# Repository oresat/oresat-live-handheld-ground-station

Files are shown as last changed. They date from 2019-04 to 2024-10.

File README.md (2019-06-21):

# Introduction
The OreSat Live Handheld Ground Station (HGS) project provides everything you need to build your own ground station capable of receiving images transmitted from OreSat in Low Earth Orbit.  HGS is designed to be inexpensive, easy to assemble, and simple to use so that it can be built by Middle and High School students.  The entire design is open source to encourage reuse and experimentation.

HGS is a portable unit built around a high gain directional antenna. Using a mobile phone application to locate OreSat, you aim the antenna to get the best possible signal. The live images are then received by the groundstation, error corrections are applied and the image is made available to any WiFi capable device through a built-in web page.

OreSat HGS act as a wifi access point providing an unsecured wireless network named "OreSatLive".  Devices identify the network as a hotspot requiring the user to sign-in for Internet access.  To view the image stream simply:
1. Connect your wifi to the "OreSatLive" network
2. Choose to sign-in when prompted
3. The OreSat Live web interface will open automatically

HGS was created for use with the OreSat mission, but it is designed to be used by any group interested in long range image transmission.  The handheld ground stations can be reused for other cubesat or balloon launches.

Once the final design is completed, users will be able to purchase all of the required parts as a kit from https://www.crowdsupply.com/

# HGS Parts List
All of the required parts to build HGS can be found in the Bill of Materials [(BOM)](BOM.md)

# Hardware Setup
Build your Handheld Ground Station kit according to the [Assembly Instructions](hgs-model/assembly-instructions/OreSat_Live_HGS_Assembly.pdf)

# Software Setup
1. [Download the SD card image oresat_hgs_14_jun_2019.img](https://drive.google.com/a/pdx.edu/uc?id=1BvP8ltkEwoBRSbCfQXceEiuxpVhkSf37&export=download)
2. Write the SD card image to a 2GB or larger card.  The [Raspberry Pi documentation](https://www.raspberrypi.org/documentation/installation/installing-images/) explains the procedure.

# Startup Procedure
1. Install the SD card in Raspberry Pi
2. Insert phone into the holder
3. Connect Raspberry Pi power cable to the USB power bank
4. Load Satellite AR app on phone and select OreSat
5. Point the ground station in the direction of OreSat
3. Connect your viewing devices to the "OreSatLive" wifi network

# Design Details
## Software Design
If you would like to build the software system from source follow the [Build Instructions](software/BUILD.md)

## Mechanical Design
You can 3D print all of the [mechanical parts](hgs-model/README.md)  

## Circuit Board Design
The integrated antenna backplane and matching network [circuit board design files](backplane/README.md)

# Related Projects
[OreSat Live](https://github.com/oresat/oresat-dxwifi-software) for software and firmware used on OreSat satellite

[Mini OreSat](https://github.com/oresat/oresat-live-mini-oresat) combines the OreSat Live software with a Raspberry Pi Zero W + Pi Camera to create platform for hobbyist and classroom experiments with high-altitude ballooning.

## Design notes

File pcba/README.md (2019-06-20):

# Backplane for Handheld Ground Station
Schematic files for the backplane, including impedence matching circuit for connecting the antenna to the rest of the components.

Schematic files created using KiCad 5.1.2.
- **.pro** to open up Kicad project
- **.kicad_pcb** for the PCB layout
- **.kicad_mod** for the individual footprints

## Microstrip Dimensions
Backplane material: FR-4 PCB material, 0.5 oz copper, 1.58 mm thick, Er 4.34 @ 1 GHz
Note: Do not remove any of the copper ground plane on the other side of the board beneath the traces.  

Microstrip widths for various impedances:
```
50 ohm
	Width:  3.05184 mm
	Length: Arbitrary

83 ohm?
	Width: 1.20938 mm
	Length: Arbitrary

140 ohm
	Width:  0.238155 mm
	Length: Arbitrary
```

## 1/4 Wave Matching Transformer Design:
	Start at connector
	Arbitrary length of 50 ohm
	Lambda/4 length (17.7623 mm) of 83.66 ohm
	Arbitrary length of 140 ohm
	End at the helix element

## Other notes
[Source for Raspberry Pi Zero footprint dimensions](http://www.electronics-lab.com/raspberry-pi-zero-footprint-and-dimensions/)\
[Source for wf-np9202 footprint dimensions](https://www.aliexpress.com/item/wireless-net-card-LAN-NIC-module-AR9271-150M-wireless-LAN-net-card-industrial-module/32746090657.html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)

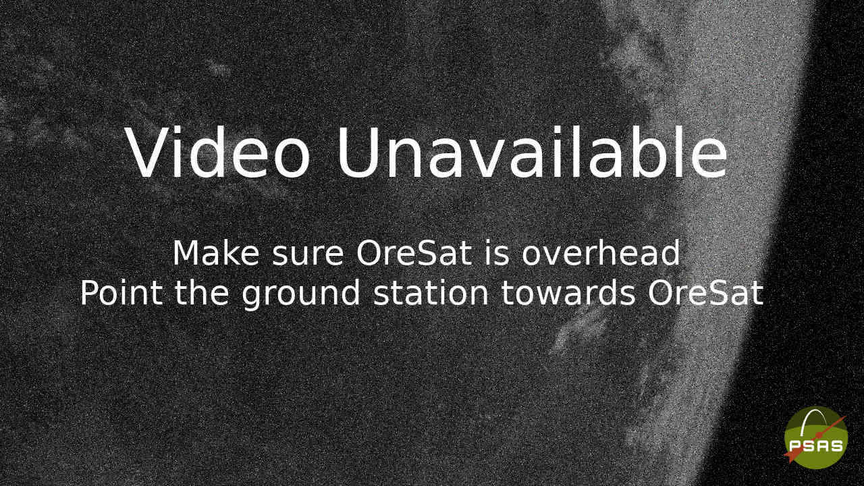
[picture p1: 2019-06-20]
software/rootfs/var/www/html/assets/img/stream_error.jpg

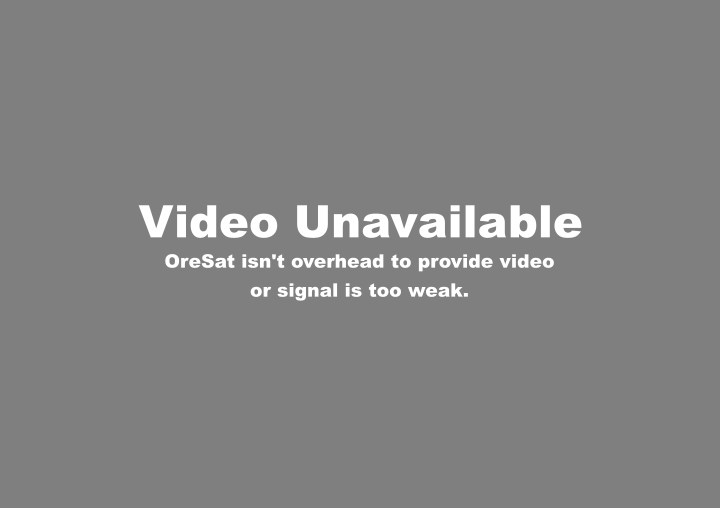
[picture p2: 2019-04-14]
software/rootfs/var/www/html/assets/img/stream_error.png

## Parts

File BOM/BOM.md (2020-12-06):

# OreSat Handheld Ground Station Bill of Materials

## Hardware
| Qty | Description | Source | Manufacturer | Part Number  |
|-----|---|---|---|---|
| 4 | #8-32 x 1 in screws and hexnuts | Home Depot | Everbilt | 460 626 |
| 4 | #8-32 x 1.5 in screws and hexnuts | Home Depot | Everbilt | 461 400 |
| 7 | #2-56 x 3/8 Nylon Screw | Frys | Waldom | FN-816-0025P |
| 7 | #2-56 Nylon Lock Nut | Frys | Waldom | FN-502-0025P |
| 7 | #2-56 Nylon hex nut | Frys | Waldom | FN-853-0025P |
| 63" | 20AWG magnet wire | Frys | Philmore | 12-1220 |

Items for easy clamping while gluing or for assembly without glue:

| Qty | Description | Source | Manufacturer | Part Number  |
|-----|---|---|---|---|
| 4 | #8-32 x 5 in Threaded Rod | Mcmaster-Carr | N/A | 91565A335 |
| 3 | #8-32 2 1/2 in Female Threaded Standoff | Mcmaster-Carr | N/A | 91115A831 |
| 2 | #8-32 Steel Hex Nut | Mcmaster-Carr | N/A | 90480A009 |

If you wish to use metric fasteners you can substitute #2-56 for M2 and #8-32 for M4

1/4-20 hex nut for tripod mounting

1.5in Hook-and-loop (velcro) adhesive backed

Foam Tape - Camper Seal 3/16in x 1 1/4in

Rubber band of your choosing

## Plastic Components
Handle

Screw Block

Phone Holder Base

Phone Holder Slide

Battery Holder

Antenna Sections (8)

Antenna Top Cap

Antenna Bottom Cap

## Electronics
Raspberry Pi Zero W

Atheros Module

USB Micro B to Atheros module custom cable 

6" USB A to Micro B power cable

5000 mAh USB power bank

## Circuit Board Components
8.2pF 0402 1% tolerance capacitor

U.FL SMD connector

75mm U.FL to U.FL coax cable

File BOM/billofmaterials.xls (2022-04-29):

PART NUMBER | DESCRIPTION | QTY. | Cost ($USD)
FASTENERS:
90480A009 | #8-32 HEX NUT | 12 | 0.198
93135A015 | #2-56 X 3/8" NYLON SCREW | 6 | 0.3468
90604A199 | #8-32 x 1" SCREW | 10 | 0.918
94812A111 | #2-56 NYLON HEX NUT | 6 | 0.4284
1/4"-20 HEX NUT | OPTIONAL: FOR TRIPOD MOUNTING | 1 | 0.0303
 | TOTAL FASTENER COST: | 1 | 1.9215
3D PRINTED PARTS:
Phone&BatteryHolderTopv2 | 3D PRINT: SLIDING PHONE HOLDER | 1 | 9.76
Phone&BatteryHolderBottomv2 | 3D PRINT: PHONE AND BATTERY HOLDER | 1 | 14.17
Handle_V3 | 3D PRINT: HANDLE | 1
HelicalAntennaSegments | 3D PRINT: ANTENNA SEGMENT 2 | 1 | 15.80
HelicalAntennaSegments | 3D PRINT: ANTENNA SEGMENT 3 | 1 | 15.85
HelicalAntennaSegments | 3D PRINT: ANTENNA SEGMENT 4 | 1 | 15.39
HelicalAntennaSegments | 3D PRINT: ANTENNA BASE (SEGMENT 1) | 1 | 17.28
Phone&BatteryHolderBasev3 | 3D PRINT: BASE TO PHONE HOLDER | 1 | 7.29
bracket | 3D PRINTED BRACKET FOR HANDLE | 1 | 7.14
 | TOTAL 3D PRINT COST: |  | 102.68
MISC:
iphone 6 | PHONE FOR USE | 1
75 MM U.FL TO U.FL COAX CABLE |  | 1
63" OF 20-GAUGE MAGNET WIRE |  | 1
MICRO USB TO WIRELESS MODULE CONNECTOR CABLE |  | 1
6" USB A TO MICRO B CABLE |  | 1
Power Bank | 5000mAh BATTERY WITH USB | 1
1.5" HOOK AND LOOP VELCRO ADHESIVE | FOR BATTERY HOLDER | 1
FOAM TAPE | FOR PHONE HOLDER | 1
RUBBER BANDS | FOR PHONE HOLDER | 2
reflectorgroundplane | OSHPARK PCB | 1
RaspberryPiZeroW | RASPBERRY PI ZERO W | 1 | 10.00
AR9271Chip | WF-NP9202 ATHEROS WIRELESS MODULE | 1

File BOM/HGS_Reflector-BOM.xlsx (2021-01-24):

Bill Of Materials for OreSat Live Handheld ground Station PCBA
Last modified: 2020/01/07
PCB version: 2.0 |  |  | P/DNP = | Place/Do Not Place (DNP is for final production boards)
BOM revision: 0 |  |  | Generic = | Any generic part with the same characteristics are OK (e.g., bypass cap)
Cnt | Part References | P/DNP | Mfg | Mfg PN | Description | Generic | Dist | Dist Part Number
4 | C1, C11, C9, C21 |  |  |  | 0603 100p
7 | C2, C5, C10, C12, C13, C17, C20 | P | Yageo | CC0603KRX5R7BB105 | 1µF ±10% 16V Ceramic Capacitor X5R 0603 | Y | Digi-Key | 311-1444-1-ND
6 | C3, C4, C6, C14, C18, C19 | P | ?? | ?? | 0402 100p | N
2 | C7, C15 | P | ?? | ?? | 0603 10n | Y
2 | C8, C16 | P | ?? | ?? | 0603 2.2u | Y
3 | E1, E2, E5 | P | Murata | BLM18GG471SZ1D | 470 Ohms @ 100Mhz 1 Signal Line Ferrite Bead 0603 200mA 1.3Ohm | Y
2 | E3, E4 | P | Murata | BLM18DN381SZ1D | 380 Ohms @ 100Mhz 1 Ferrite Bead 0603 850mA | Y
1 | J1 | P | TE Connectivity | 1909763-1 | U.FL (UMCC) Connector Jack | Y | Digi-Key | A118077CT-ND
1 | J2 | P | ?? | PRT-00587 | USB type Mini-B Connector | Y | Mouser | 474-PRT-00587
1 | J3 | P | JST | SM06B-SRSS-TB(LF)(SN) | Connector Header SMT, RA 6 pos 1.00mm | Y
2 | J5, J6 | P | Amphenol | 132134-10 | SMA Connector Jack, Female Socket 50Ohm SMT | Y | Mouser | 523-132134-10
1 | J7 | P | SparkFun | PRT-09011 | SparkFun Accessories USB Female Type A SMD Connector | Y | Mouser | 474-PRT-09011
2 | L1, L2 | P | ?? | ?? | L3216C 10n | N
2 | L3, L4 | P | ?? | ?? | L3216C 8n | N
2 | LED1, LED2 | P | Rohm | SML-E12M8WT86 | Green 572nm LED Indication - Discrete 2.2V 0603 | Y | Digi-Key | 511-1584-1-ND
1 | PCBA1 | P | Aliexpress | WF-NP9202WF | AR9721 based WiFi transciever | N
1 | PCBA2 | P | Raspberry Pi | RASP_PI_0WPI_0W | Raspberry Pi Zero W | N
5 | R1, R2, R3, R5, R6 | P | Yageo | RC0603JR-070RL | RES SMD 0 OHM JUMPER 1/10W 0603 | Y | Digi-Key | 311-0.0GRCT-ND
1 | R4 | P | ?? | ?? | 0402 150 | Y
2 | R7, R9 | P | Yageo | RC0603FR-071KL | RES SMD 1K OHM 1% 1/10W 0603 | Y | Digi-Key | 311-1.00KHRCT-ND
2 | U1, U2 | P | TI | LP2985IM5X-3.3/NOPB | Linear Voltage Regulator IC 1 Output 150mA SOT-23-5 | N | Digi-Key | 296-18476-2-ND
1 | U3 | P | Mini-Circuits | NCS3-272+ | Signal Conditioning 1:3 LTCC Transformer, 2250 - 2725 Mhz, 50 ohms | N
2 | U4, U5 | P | Qorvo | QPQ1907SR | Signal Conditioning Coexist BAW FILTER 2402.5 - 2481.5 Mhz | N
2 | U6, U7 | P | Qorvo? | TP3M9037? | LNA? | N | Mouser | 772-TQP3M9037
1 | CABLE1 | P | JST | A06SR06SR30K51A | 6 Position Cable Assembly Rectangular Socket to Socket, Reversed 0.167' (50.80mm, 2.00") | Y | Digi-Key | 455-2999-ND
Rev | Date | Notes
2.0r0 | 2020-01-07 | First revision of the BOM for v2 PCB

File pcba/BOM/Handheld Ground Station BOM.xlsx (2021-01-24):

Count | Ref Des | Value | MFR | MPN | Description | Size | Generic? | Digi-Key Part No. | Mouser Part No. | Mini-Circuits Link
4 | C1, C11, C9, C21 | 100 pF | Murata | GCM1885C1H101JA16D | CAP CER 100PF 50V C0G/NP0 0603 | 0603 | Y | 490-4767-1-ND
7 | C2, C5, C10, C12, C13, C17, C20 | 1 uF | Yageo | CC0603KRX5R7BB105 | CAP CER 1UF 16V X5R 0603 | 0603 | Y | 311-1444-1-ND
6 | C3, C4, C6, C14, C18, C19 | 100 pF | Murata | GCM1555C1H101JA16D | CAP CER 100PF 50V C0G/NP0 0402 | 0402 | Y | 490-10669-1-ND
2 | C7, C15 | 10 nF | Murata | GCD188R71H103KA01D | CAP CER 10000PF 50V X7R 0603 | 0603 | Y | 490-17738-1-ND
2 | C8, C16 | 2.2 uF | Murata | GRM188R61E225KA12D | CAP CER 2.2UF 25V X5R 0603 | 0603 | Y | 490-10731-1-ND
3 | E1, E2, E5 | BLM18GG471SZ1D | Murata | BLM18GG471SZ1D | FERRITE BEAD 470 OHM 0603 1LN | 0603 | Y | 490-16658-1-ND
2 | E3, E4 | BLM18DN381SZ1D | Murata | BLM18DN381SZ1D | FERRITEBEAD SMD Z100MHZ=380OHM 8 | 0603 | Y | 490-18574-1-ND
1 | J1 | U.FL | TE Connectivity | 1909763-1 | CONN UMCC JACK STR 50OHM SMD |  | Y | A118077CT-ND
1 | J2 | USB_MINI-B_SMT | SparkFun | PRT-00587 | USB Mini-B SMD Connector |  | Y |  | 474-PRT-00587
1 | J3 | SM06B-SRSS-TB(LF)(SN) | JST Sales America Inc. | SM06B-SRSS-TB(LF)(SN) | CONN HEADER SMD R/A 6POS 1MM |  | Y | 455-1806-1-ND
2 | J5, J6 | 132134-10 | Amphenol RF | 132134-10 | CONN SMA JACK STR 50 OHM SMD |  | Y | ARF2755-ND
1 | J7 |  | SparkFun | PRT-09011 | USB Female Type A SMD Connector |  | Y |  | 474-PRT-09011
2 | L1, L2 | 10nH | Pulse Electronics Network | PE-1206CD100JTT | FIXED IND 10NH 1A 80 MOHM SMD | L3216C | Y | 1840-1138-1-ND
2 | L3, L4 | 8nH | Murata | LQW31HN8N8J03L | Fixed Inductors 1206 8.8nH +/-5% | L3216C | Y |  | 81-LQW31HN8N8J03L
2 | LED1, LED2 | GREEN | Rohm Semiconductor | SML-E12M8WT86 | LED GREEN DIFFUSED 0603 SMD | 0603 | Y | 511-1584-1-ND
1 | PCBA1 | WF-NP9202WF | Aliexpress | WF-NP9202WF | AR9721 based WiFi transciever |  | N
1 | PCBA2 | RASP_PI_0W | Raspberry Pi | RASP_PI_0WPI_0W | Raspberry Pi Zero W |  | N
5 | R1, R2, R3, R5, R6 | 0 | Yageo | RC0603JR-070RL | RES SMD 0 OHM JUMPER 1/10W 0603 | 0603 | Y | 311-0.0GRCT-ND
1 | R4 | 150 | Panasonic Electronic Components | ERJ-2RKF1500X | RES SMD 150 OHM 1% 1/10W 0402 | 0402 | Y | P150LCT-ND
2 | R7, R9 | 1k | Yageo | RC0603FR-071KL | RES SMD 1K OHM 1% 1/10W 0603 | 0603 | Y | 311-1.00KHRCT-ND
2 | U1, U2 | LP2985XX-N | TI | LP2985IM5X-3.3/NOPB | IC REG LINEAR 3.3V 150MA SOT23-5 |  | N | LP2985IM5X-3.3/NOPBCT-ND
1 | U3 | NCS3-272+ | Mini-Circuits | NCS3-272+ | 1:3 LTCC Transformer, 2250 - 2725 MHz, 50Ω |  | N |  |  | https://www.minicircuits.com/WebStore/dashboard.html?model=NCS3-272%2B
2 | U4, U5 | QPQ1907 | Qorvo | QPQ1907SR | Signal Conditioning Coexist BAW FILTER |  | N |  | 772-QPQ1907SR
2 | U6, U7 | LNA-TQP3M9037 | Qorvo | TQP3M9037 | RF Amplifier 1.5-2.7GHz |  | N |  | 772-TQP3M9037
1 | CABLE1 |  | JST Sales America Inc. | A06SR06SR30K51A | JUMPER 06SR-3S - 06SR-3S 2" |  | N | 455-2999-ND

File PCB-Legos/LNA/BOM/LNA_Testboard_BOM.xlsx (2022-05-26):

HGS LNA Test Board
Last modified: 2022/05/22
PCB version: 1.0
BOM revision: 0
Cnt | Part References | P/DNP | Mfg | Mfg PN | Description | Generic | Dist | Dist Part Number
6 | C2,C6,C7,C9,C13,C14 | P | Murata | GRM0335C1E101JA01D | 0603 100p | Y | Mouser | 81-GRM0335C1E101JA1D
5 | C3,C8,C10,C15,C17 | P | Yageo | CC0603KRX5R7BB105 | 1µF ±10% 16V Ceramic Capacitor X5R 0603 | Y | Digi-Key | 311-1444-1-ND
2 | C4,C11 | P | TDK | C0603X5R1A103M030BA | 0603 10n | Y | Mouser | 810-C0603X5R1A103M
2 | C5,C12 | P | TDK | C1608X7S1C225K080AE | 0603 2.2u | Y | Mouser | 810-C1608X7S1C225K08
2 | E1, E2, | P | Murata | BLM18GG471SZ1D | 470 Ohms @ 100Mhz 1 Signal Line Ferrite Bead 0603 200mA 1.3Ohm | Y | Mouser | 81-BLM18GG471SZ1D
1 | J4 | P | SparkFun | PRT-00587 | USB Mini-B SMD Connector | Y | Mouser | 474-PRT-00587
3 | J1,J2,J3 | P | Cinch | 142-0701-801 | SMA 50 Ohm End Launch Jack Receptacle -Round Contact | Y | Mouser | 530-142-0701-851
2 | L2, L4 | P |  |  | L3216C 10n | N
2 | L1, L3 | P |  |  | L3216C 8n | N
1 | LED1 | P | Rohm | SML-E12M8WT86 | Green 572nm LED Indication - Discrete 2.2V 0603 | Y | Digi-Key | 511-1584-1-ND
6 | R1,R2,R3,R4,R5,R7 | P | Yageo | RC0603JR-070RL | RES SMD 0 OHM JUMPER 1/10W 0603 | Y | Digi-Key | 311-0.0GRCT-ND
1 | R6 | P | Yageo | RC0603FR-071KL | RES SMD 1K OHM 1% 1/10W 0603 | Y | Digi-Key | 311-1.00KHRCT-ND
2 | U1, U2 | P | TI | LP2985AIM5-3.3/NOPB | Linear Voltage Regulator IC 1 Output 150mA SOT-23-5 | N | Mouser | 926-2985AIM53.3/NOPB
2 | U3, U6 | P | Qorvo | QPQ1907SR | Signal Conditioning Coexist BAW FILTER 2402.5 - 2481.5 Mhz | N | Mouser | 772-QPQ1907SR
2 | U2, U5 | P | Qorvo | TQP3M9037 | LNA | N | Mouser | 772-TQP3M9037
Rev | Date | Notes
1 | 2022-05-22

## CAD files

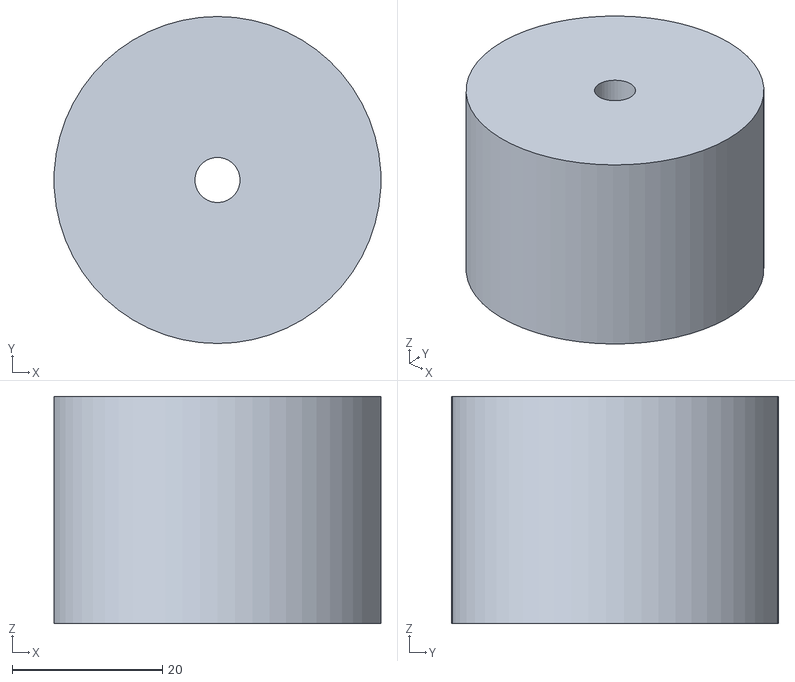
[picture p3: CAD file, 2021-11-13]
build/HelicalAntennaSegmentCap.STL
43.4 x 43.5 x 30.2

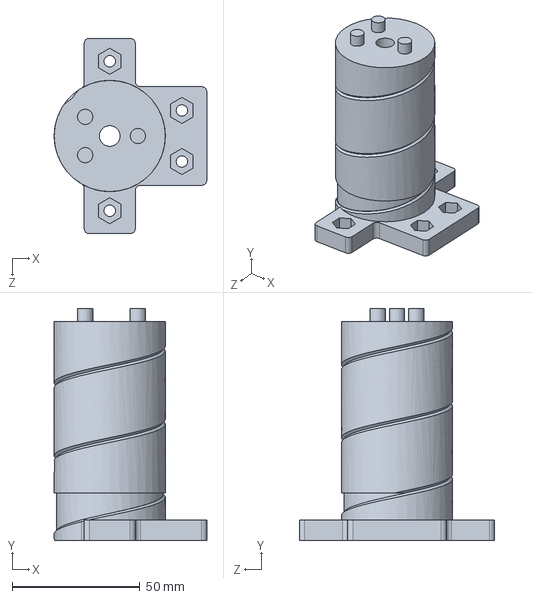
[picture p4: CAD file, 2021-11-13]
mechanical/antennaSegments/helicalAntennaSegment.SLDPRT
59.8 x 90.8 x 76.5 mm

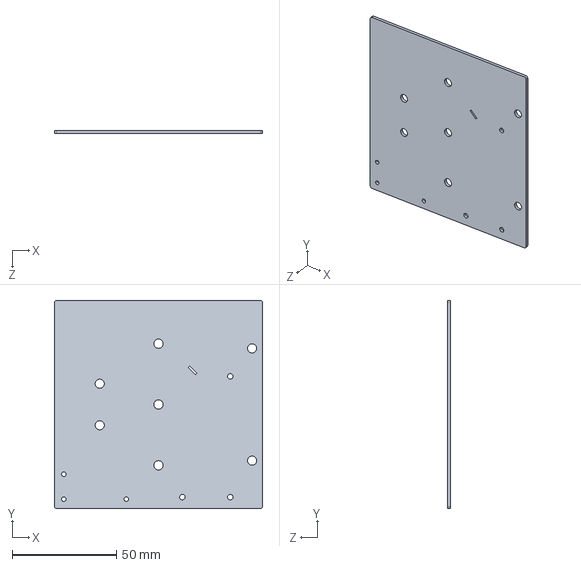
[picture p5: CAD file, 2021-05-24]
mechanical/electricalComponents/groundStationBackplane.SLDPRT
100.0 x 100.0 x 1.60 mm

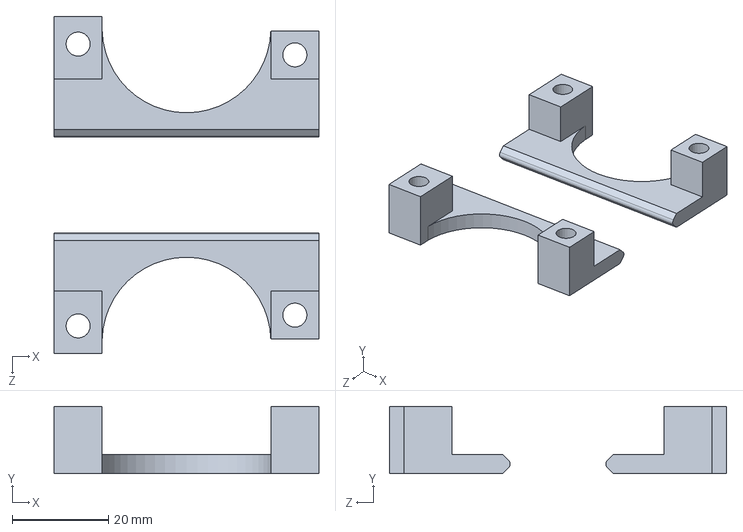
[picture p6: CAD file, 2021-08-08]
mechanical/handleAssembly/phoneClampBracket.SLDPRT
55.0 x 14.0 x 70.0 mm

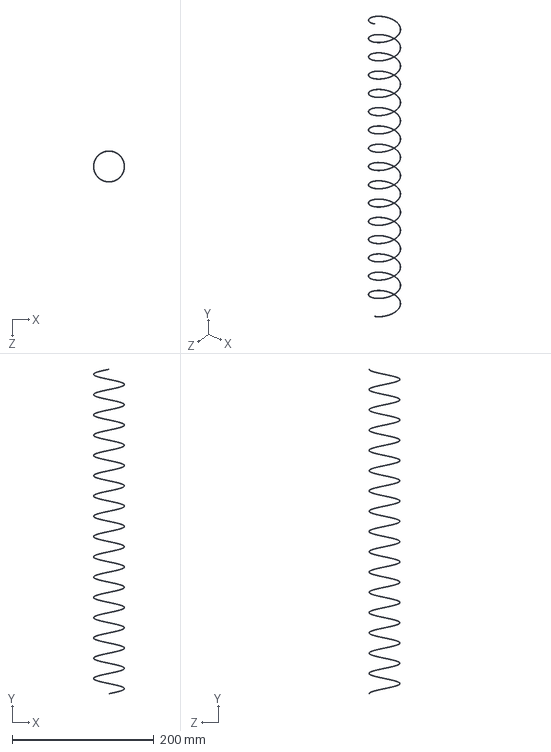
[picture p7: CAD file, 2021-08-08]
mechanical/modelParts/helicalAntenna.SLDPRT
44.3 x 458.4 x 44.3 mm

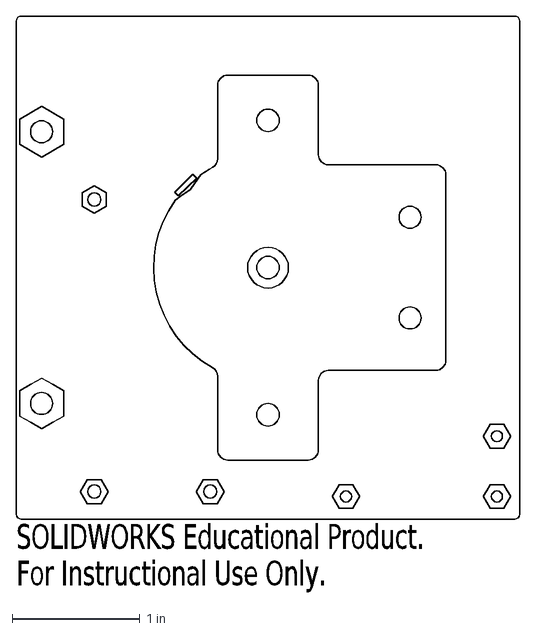
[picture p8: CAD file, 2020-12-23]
pcba/DXF/keepoutAntennaSide.DXF
SOLIDWORKS Educational Product.
For Instructional Use Only.

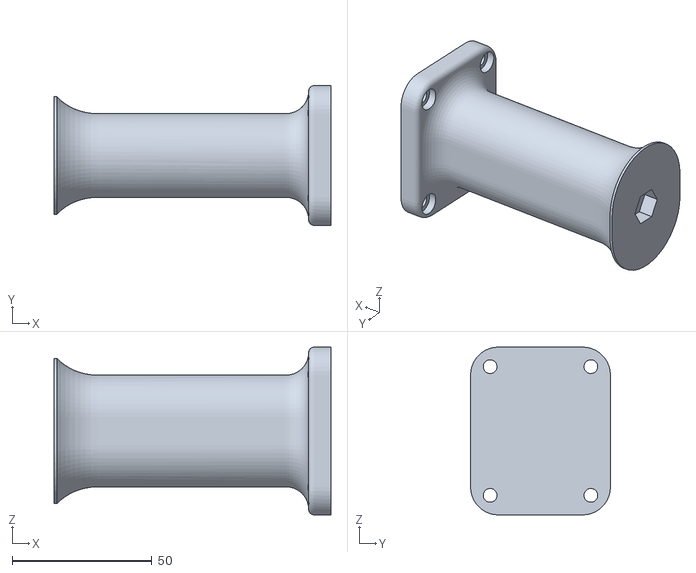
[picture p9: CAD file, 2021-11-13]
build/handle.STL
99.0 x 50.0 x 60.0

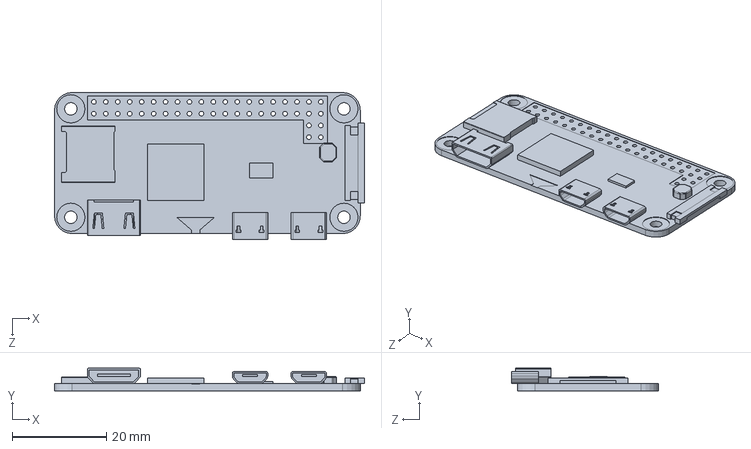
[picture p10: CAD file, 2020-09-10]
mechanical/electricalComponents/RaspberryPiZeroW.SLDPRT
65.9 x 4.80 x 31.2 mm

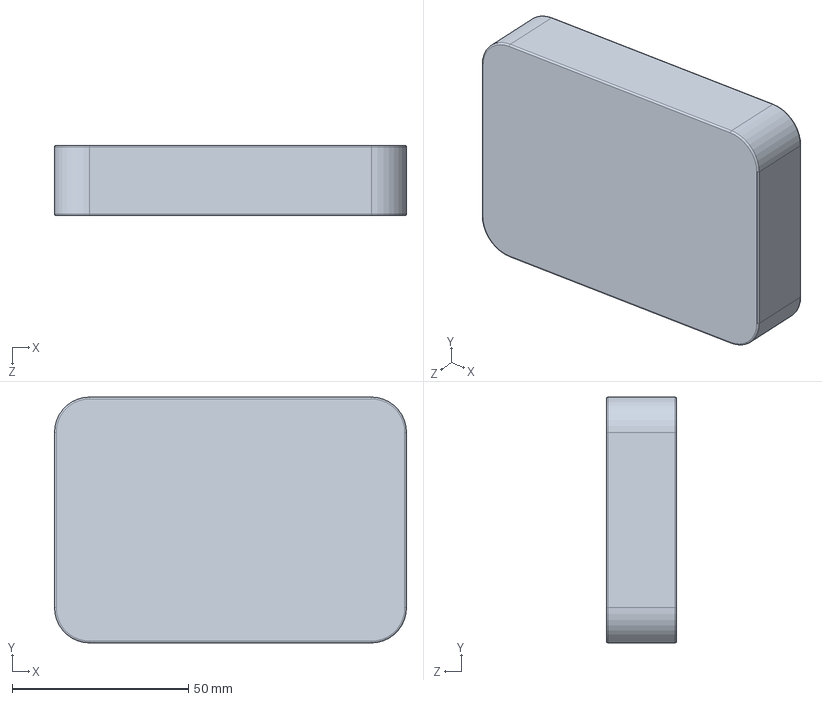
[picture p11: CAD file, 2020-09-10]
mechanical/modelParts/batterypack.SLDPRT
100.0 x 69.8 x 20.0 mm

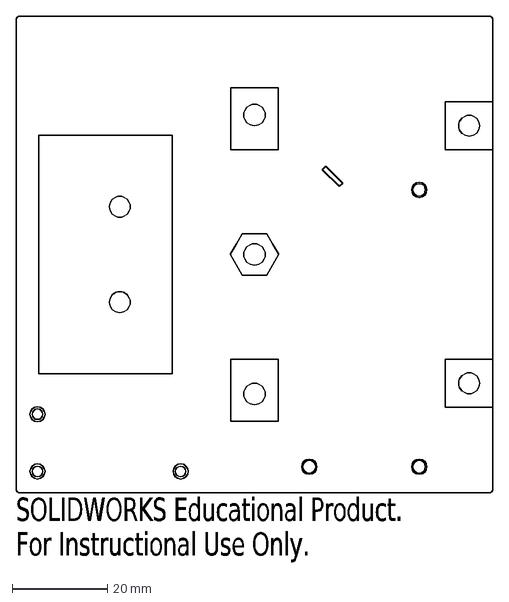
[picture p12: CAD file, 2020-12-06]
pcba/DXF/keepout.DXF
SOLIDWORKS Educational Product.
For Instructional Use Only.

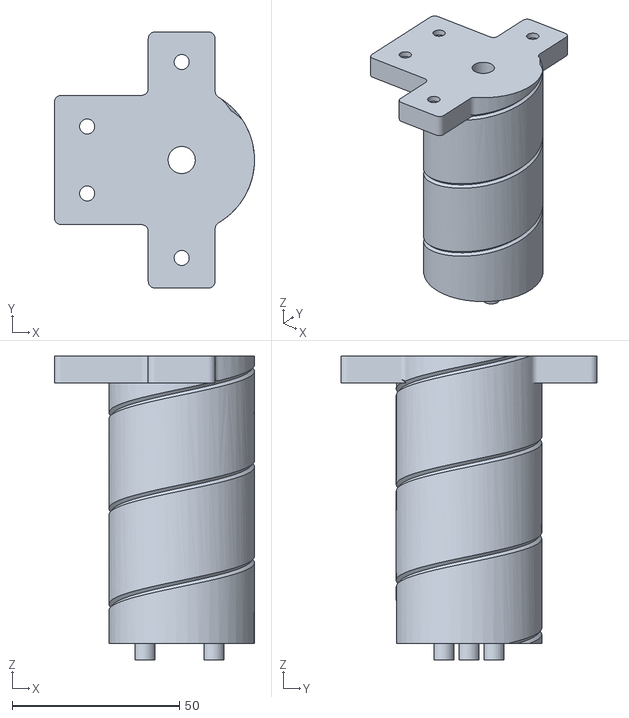
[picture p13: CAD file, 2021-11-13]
build/helicalAntennaSegmentBase.STL
59.7 x 76.5 x 90.8

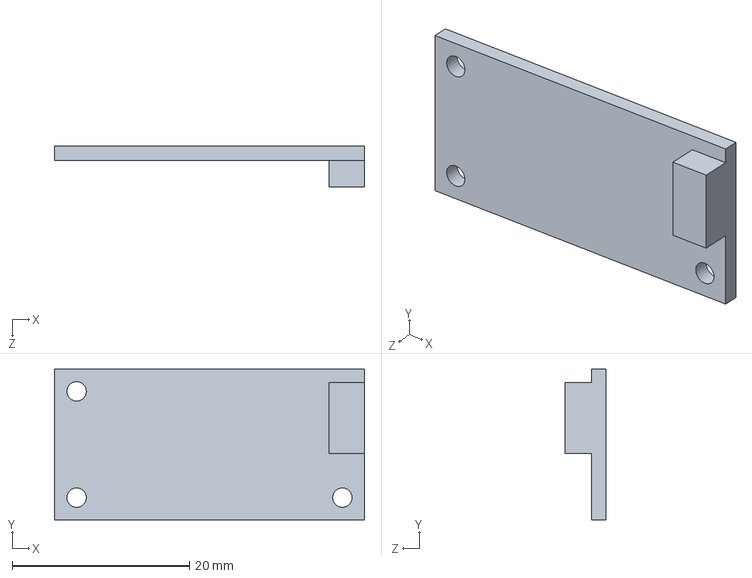
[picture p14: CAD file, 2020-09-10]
mechanical/electricalComponents/AR9271Chip.SLDPRT
35.0 x 17.0 x 4.60 mm

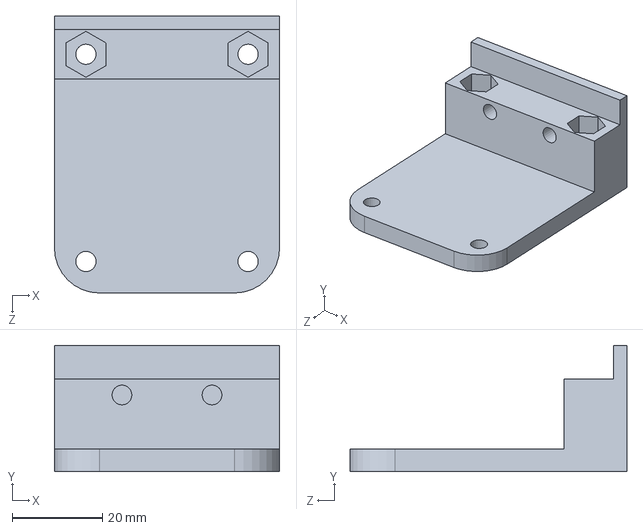
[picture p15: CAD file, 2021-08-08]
mechanical/handleAssembly/bracket.SLDPRT
50.0 x 28.0 x 61.5 mm

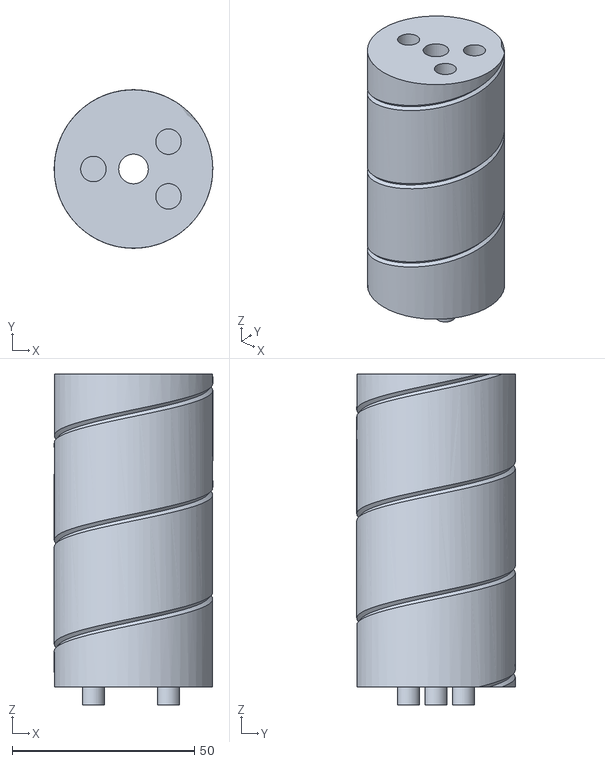
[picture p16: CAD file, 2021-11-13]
build/helicalAntennaSegmentStandard.STL
43.5 x 43.5 x 90.8

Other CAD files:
mechanical/antennaSegments/helicalAntennaSegmentCap.SLDPRT
mechanical/handleAssembly/handle.SLDPRT
mechanical/handleAssembly/handleBracketBottom.SLDPRT
build/bracket.STL
build/handleBracketBottom.STL
build/handleBracketTop.STL
build/helicalAntennaSegment-22.STL
build/phoneClampBracket-1.STL
mechanical/COTS/#8-32 nylock.sldprt
mechanical/COTS/90604A199_PAN HEAD COMBINATION DRIVE MACHINE SCREW.SLDPRT
mechanical/COTS/92319A679_FEM THRDED HEX STANDOFF.SLDPRT
mechanical/COTS/93135A015_NYLON PAN HEAD MACHINE SCREW.SLDPRT
mechanical/COTS/93225A675_Aluminum Threaded Rod.SLDPRT
mechanical/COTS/94435A509_ALUMINUM THREADED ROD.SLDPRT
mechanical/COTS/94639A460_NYLON UNTHREADED SPACERS.SLDPRT
mechanical/COTS/94812A111_NYLON 6-6 HEX NUT.SLDPRT
mechanical/handleAssembly/handleBracketTop.SLDPRT

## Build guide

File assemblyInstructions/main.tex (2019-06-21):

% Date of the last edit of these instructions
\def \lastedit{June 20, 2019}

\documentclass[paper=a4,parskip=full+]{scrartcl}
\usepackage[utf8]{inputenc}
\usepackage{titletoc}
\usepackage[margin=1in]{geometry}
\usepackage{float}
\usepackage{parskip}
\usepackage{graphicx}
\graphicspath{ {Images/} }

\title{OreSat Live HGS Assembly}
\date{Last Edited: \lastedit}

\begin{document}

\maketitle
\tableofcontents

\section{Introduction}
This document provides instructions for assembling the Handheld Ground Station with a kit.
\section{Overview of Required Materials}
\subsection{The Kit}
The kit comes with the following items:
\begin{itemize}
    \item Back-plane Circuit board
    \item 75mm U.FL to U.FL Coax Cable
    \item 63" of 20-gauge Magnet Wire
    \item Raspberry Pi Zero W
    \item WF-NP9202 Atheros Wireless Module
    \item Micro USB to Wireless Module Connector Cable
    \item 6" USB A to Micro B Cable
    \item 5000mAh Battery with USB
    \item $1/4$"-20 nut for tripod mounting
    \item 1.5" Hook-and-loop Velcro (adhesive-backed)
    \item Plastic Components
    \begin{itemize}
        \item Handle
        \item Screw Block
        \item Phone Holder Base
        \item Phone Holder Slide
        \item Battery Holder
        \item Antenna Sections x4
        \item Antenna Top Cap
        \item Antenna Bottom Cap
    \end{itemize}
\end{itemize}

\subsubsection{Board Check}
Please check that the backplane board comes with both a U.FL connector and a 8.2pF capacitor already soldered on to the board. 
% PICTURE HERE of microstrip, U.FL connector and pF cap soldered on board

\subsection{Parts Not Provided}
The parts below are not a part of the kit but still needed to assemble the HGS.\\
\textbf{*Note: You DO NOT have to use the sources specified in these tables.}
\begin{table}[H]
    \footnotesize
    \begin{tabular}{|l|l|l|l|l|}
        \hline
        Quantity & Description & Source & Manufacturer & Part Number\\
        \hline
        \hline
        4 & \#8-32 x 1" Screws and Hex Nuts & Home Depot & Everbilt & 460 626 \\
        \hline
        4 & \#8-32 x 1.5" Screws and Hex Nuts & Home Depot & Everbilt & 461 400 \\
        \hline
        7 & \#2-56 x 3/8 Nylon Screw & Frys & Waldom & FN-816-0025P \\
        \hline
        7 & \#2-56 Nylon Lock Nut & Frys & Waldom & FN-502-0025P \\
        \hline
        7 & \#2-56 Nylon Hex Nut & Frys & Waldom & FN-853-0025P \\
        \hline
        & Foam Tape - Camper Seal 3/16" x 1 1/4" & & & \\
        \hline
        1 & Rubber Band of your choosing & & & \\
        \hline
        
    \end{tabular}
    \label{tab:my_label}
\end{table}

\noindent The following are optional items for easy clamping while gluing or assembly without glue:

\begin{table}[H]
    \footnotesize
    \begin{tabular}{|l|l|l|l|l|}
    \hline
    Quantity & Description & Source & Manufacturer & Part Number\\
    \hline
    \hline
    1 & \#8-32 x 18 in threaded rod & Home Depot & & \\
    \hline 
    1 & 1/8in x 1 in fender washer & Home Depot & Everbilt & 210 364 \\
    \hline 
    1 & \#8-32 wing nuts & Home Depot & Everbilt & 934 917 \\
    \hline 
    \end{tabular}
\end{table}

\noindent You can substitute \#2-56 for M2 and \#8-32 for M4.

\newpage
\section{Assembly Instructions}
Do these things!
\subsection{Overview}
The core of the HGS is the circuit board/antenna back-plane, all the other components are in some way attached to it. The main electrical component we are concerned with is the wire wrapping the main antenna. It is soldered on the board to an impedance matching strip, strung through a hole in the board, wrapped around the antenna, and epoxied under a cap at the tip. For this reason the initial steps must be done in a particular order to ensure ease of assembly.

\subsection{Assemble antenna segments (no caps)}
First we will epoxy together the four antenna segments, without the end-caps.

(A threaded rod may be used to replace the epoxy. If using a threaded rod, ignore the sections about epoxying things, and in the section about winding the wire, use the threaded rod to hold everything together other than the cap, and clamp down the rod once the wire is wound.)

(For each section using epoxy, follow the manufacturers instructions for mixing, usage, and cure times. Make sure not to mix so much at one time that it starts to set before you have time to apply it all!)

Mix together a small batch of epoxy and apply it liberally to the end of one of the antenna segments, then insert the peg of another segment and apply pressure until the epoxy has set. Repeat until all four sections are connected as one antenna.

Make sure to wipe off any excess epoxy after clamping, to avoid filling the grooves.

\begin{figure}[H]
    \centering
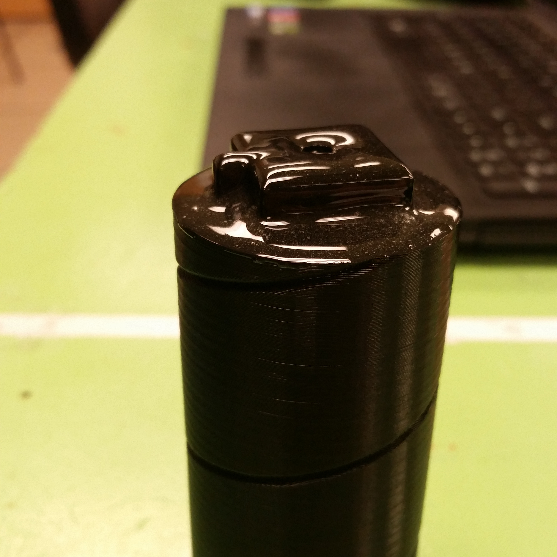
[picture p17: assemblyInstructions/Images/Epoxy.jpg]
     
    %Photo of epoxy covered antenna cap.
\end{figure}

%PHOTO OF ASSEMBLED ANTENNA

\subsection{Solder antenna wire onto micro-strip pad}
Solder one end of your wire to the bare end of the micro-strip, holding the wire perpendicular to the micro-strip. Snip off any excess wire.

Stick the rest of the wire through the nearby hole to the other side of the board for winding later.

%PHOTO HERE OF SOLDERED BOARD CLOSEUP

\subsection{Epoxy antenna to circuit board}
(Skip this section if using a threaded rod.)

Apply epoxy liberally to the peg end of the antenna, and the hollow end of the antenna clamp, push the antenna through the board, leaving the antenna on the side opposite the micro-strip, put the clamp piece on the end of the peg, sandwiching the circuit board, and clamp until the epoxy is set.

%PHOTO OF BOARD WITH ANTENNA

\subsection{Wind antenna with wire}
Take the antenna, and pulling tight against the soldered end, wrap the wire around the antenna rod, following the groove.

When the wire reaches the top, push it into the groove at the top around the tie-off peg and pull tight. (See photo.)

\begin{figure}[H]
    \centering
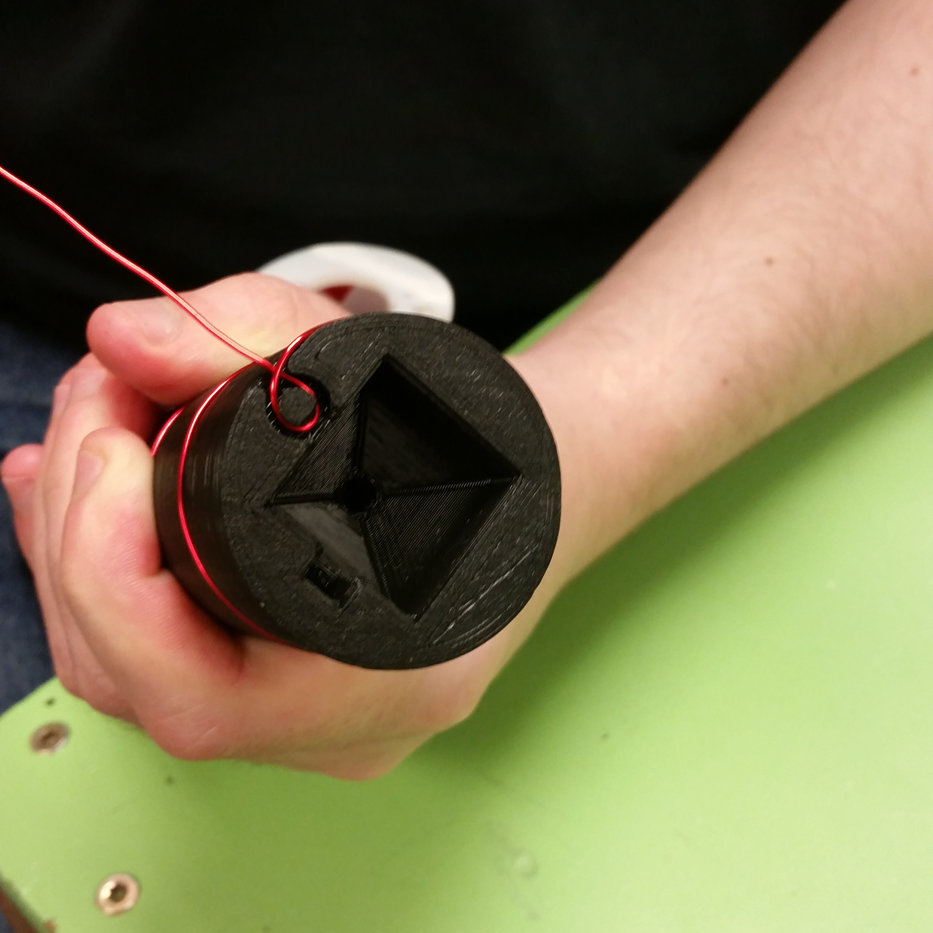
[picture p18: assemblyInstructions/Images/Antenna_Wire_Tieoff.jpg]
     %Photo of wire tie-off.
\end{figure}

\noindent With wire tightly wrapped, apply epoxy liberally to the end of the antenna cap piece, and clamp down onto the tip of the antenna until the epoxy is cured to hold down the antenna.

Snip off any excess wire.

%PHOTO OF FULLY ASSEMBLED ANTENNA

\subsection{Attach plastic and electronic components}
Now that the antenna is attached, next we'll add the electrical components, and other 3D printed parts.

Start by adding the electronics: The Raspberry Pi, and the Atheros Wifi Module. Use the \#2-56 nuts and bolts, along with nylon standoffs to attach them to the side of the board opposite the antenna in the locations marked on the board. (In the future this will be referred to as the "back" of the board.)

%PHOTO OF BOARD WITH ELECTRICAL COMPONENTS INSTALLED

Plug the U.FL connector into the Atheros and the end of the micro-strip.

%PHOTO OF ENDS OF U.FL PLUGGED IN

Next with the \#8-32 x 1.5" screws, install the Handle, and on top of it the Battery Holder, using the square Handle Clamp piece to sandwich the board. The Handle itself and the Battery Holder go on the back of the board, with the Clamp piece on the front.

Install the Phone Holder Base above the handle, on the back of the board, with the open slot facing up using the \#8-32 x 1" screws.

%PHOTO OF HANDLE WITH BATTERY HOLDER INSTALLED

Install the sticky-backed foam into the faces the top and bottom of the Phone Holders to grip the phone, then slide the Phone Holder Top into the slot.

Wrap a rubber band between the top and bottom phone holder pieces to hold them together and hold the phone when in use.

Apply the Velcro to the top of the Battery Holder, and the Battery itself, as shown in picture.

\begin{figure}[H]
    \centering
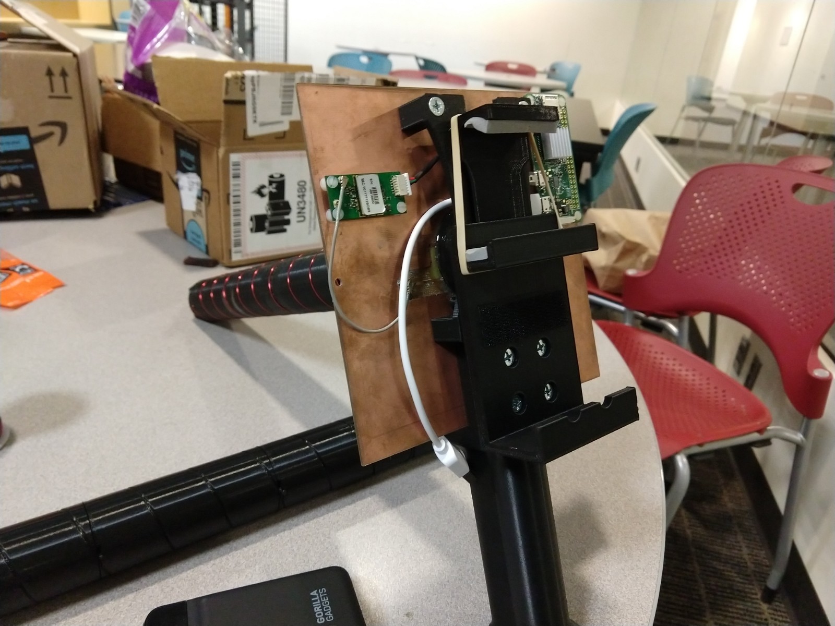
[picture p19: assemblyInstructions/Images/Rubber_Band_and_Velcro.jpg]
     %Photo of phone and battery holders with Velcro and rubber bands installed.
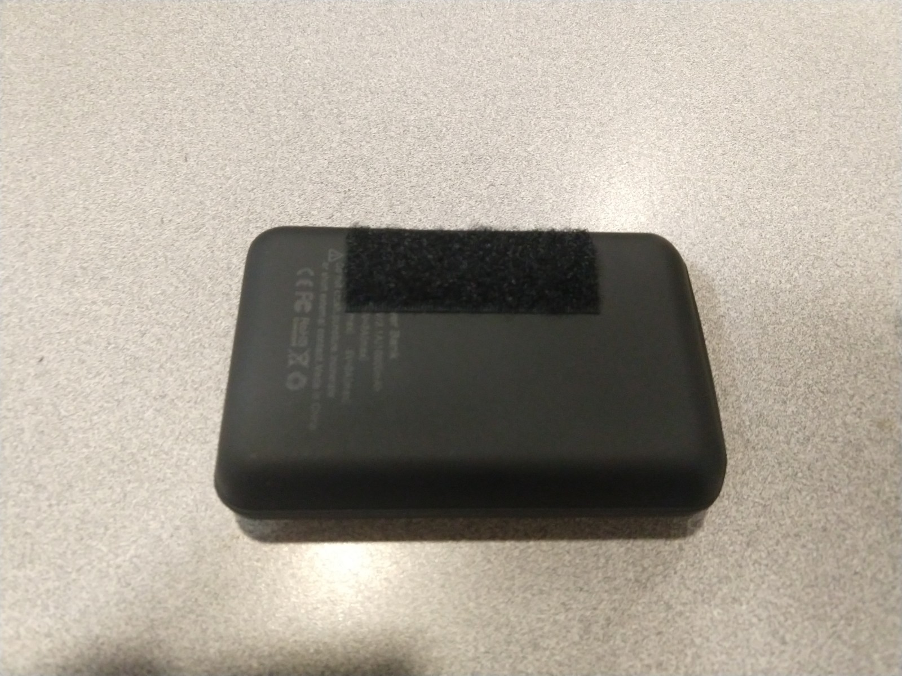
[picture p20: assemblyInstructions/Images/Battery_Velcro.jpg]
     %Photo battery with Velcro installed.
\end{figure}

Then place the battery into the holder and rock forward to install. (Do not plug into the Raspberry Pi until ready to test!)

\begin{figure}[H]
    \centering
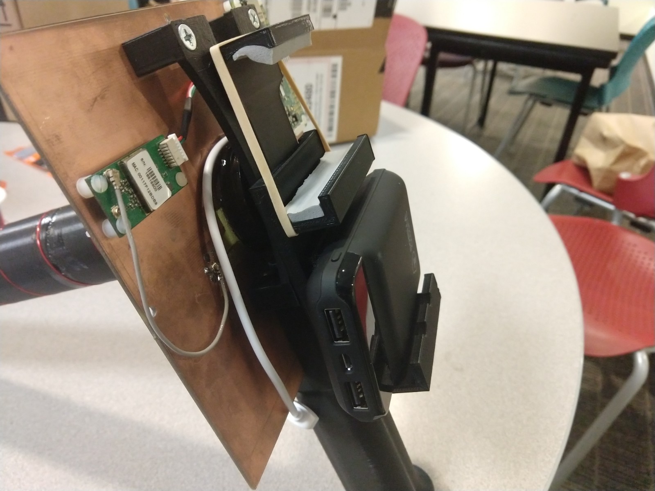
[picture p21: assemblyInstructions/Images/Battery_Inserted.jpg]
     %Photo of Battery Holder with Battery installed.
\end{figure}

For usage, simply lift the top sliding section of the phone holder, and insert your phone, try to keep the power button clear of the clamp!

\begin{figure}[H]
    \centering
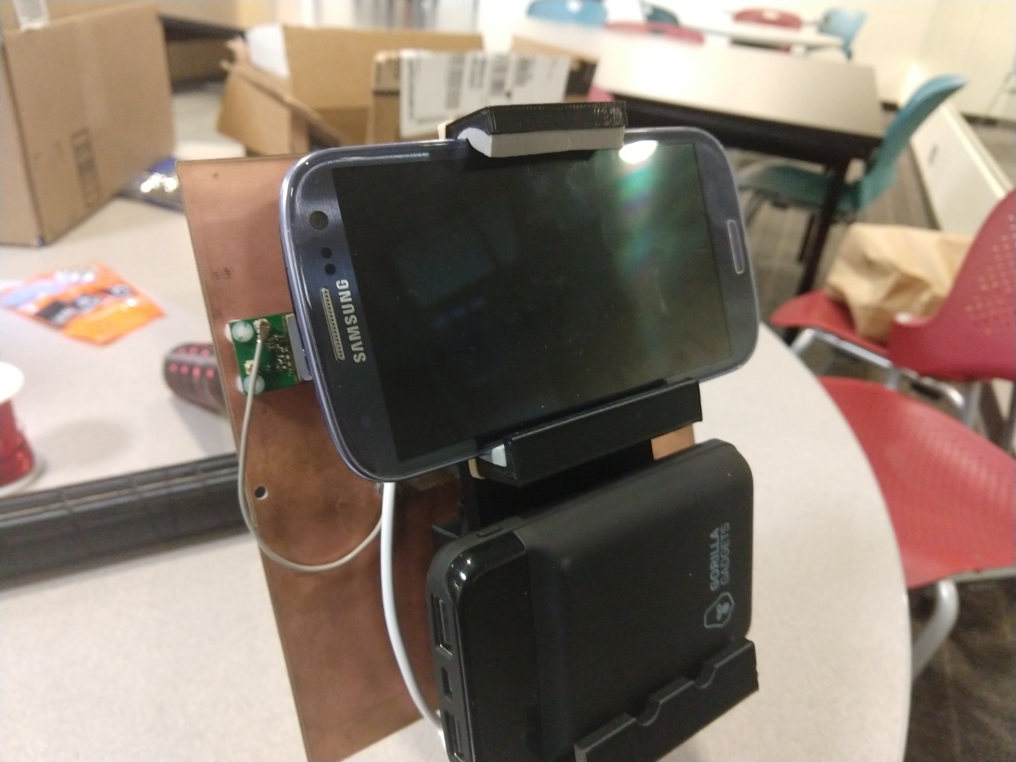
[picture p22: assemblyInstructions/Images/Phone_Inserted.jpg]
     %Photo of Full assembly with phone inserted.
\end{figure}

Congratulations, assembly is complete! Make sure to test the full assembly to make sure the electrical connections are good, and you can connect to the access point and view the webpage.

\end{document}

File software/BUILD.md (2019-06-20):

# Development Hardware
Some packages will need to be installed, which will require Internet access.  We recommend developing on a Raspberry Pi version which has onboard Ethernet.
Alternately, you can use a USB Ethernet dongle on a Raspberry Pi Zero W.  A USB to serial cable such as [Adafruit product 954](https://www.adafruit.com/product/954) is also recommended.

# Theory of Operation
On boot up /etc/rc.local calls /root/oresat_hgs.sh

oresat_hgs.sh puts the USB AR9721 wifi module into monitor mode on channel 3, then starts wifibroadcast rx and jpeg_stream_rx_stdin_write_to_file.py.

jpeg_stream_rx_stdin_write_to_file.py reads stdin searching for a start of image preamble of 10 or more \AA characters.  Once the preamble has completed the OreSat Live image transfer header is processed to determine the length and MD5 hash of the image.  If the computed MD5 hash of the recieved image matches the transmitted hash the file is written to /tmp/latest.jpg  

OreSat HGS is configured to act as a wifi access point providing an unsecured wireless network named "OreSatLive".  Users wanting to view the OreSat Live image stream will connect to this network.  The DNS, DHCP, and HTTP server settings have been configured so that clients connecting will identify the network as a hotspot requiring the user to sign-in for Internet access.  When the user chooses to sign-in the are presented with the OreSat Live web interface. 

The OreSat Live web site is hosted by the nginx web server with the conntet stored at /var/www/html/  A symlink for /tmp/latest.jpg to /var/www/html/latest.jpg connects the web server to the latest available image.

The web page being served to the clients requests latest.jpg once per second.

# Install Raspbian on SD Card
Download [2018-11-13-raspbian-stretch-lite.img](https://downloads.raspberrypi.org/raspbian_lite/images/raspbian_lite-2018-11-15/2018-11-13-raspbian-stretch-lite.zip)

Install the Raspian Lite image onto a 2GB or larger SD card.  The Raspberry Pi documentation explains the proceedure:
https://www.raspberrypi.org/documentation/installation/installing-images/

# Copy Git content
This Git repository is structured like the file system on the SD card.  Copy the files in the repo to the same location on your SD card.

# Boot configuration
Be sure to copy /boot/config.txt from the Git repo to the boot partition on your SD card.  The following lines should appear at the end of the file: 
```
dtoverlay=pi3-disable-bt
gpu_mem=256
enable_uart=1
```

# Enable SSH
```
sudo raspi-config
choose interface options
enable ssh
```

# Enable serial console (optional)
Having access to a serial console can be handy for debug.  Connect a [USB serial cable](https://elinux.org/RPi_Serial_Connection) to the Raspberry Pi.

You will need to use terminal emulator software such as `screen` or `minicom` to access the serial console.

```
sudo screen /dev/ttyUSB0 115200
```

# Compile wifibroadcast
```
apt-get install libpcap-dev
cd /root/wifibroadcast
make
```

# dnsmasq DNS + DHCP server
```
sudo apt install dnsmasq
sudo systemctl start dnsmasq
```

# NginX web server
```
sudo apt install nginx
ln -s /etc/nginx/sites-available/oresat_hgs /etc/nginx/sites-enabled/
rm /etc/nginx/sites-enabled/default
```

# Enable HostAP
```
sudo apt install hostapd
sudo systemctl unmask hostapd
sudo systemctl enable hostapd
sudo systemctl start hostapd
```

**Your ground station should now be properly configured and start automatically on the next reboot.**

# Useful Notes
## Saving a minimal-sized SD card image
[Download PiShrink](https://github.com/Drewsif/PiShrink)
```
dd bs=8M if=/dev/mmcblk0 of=~/oresat_hgs_raw.img
sudo pishrink.sh ~/oresat_hgs_raw.img ~/oresat_hgs.img
```

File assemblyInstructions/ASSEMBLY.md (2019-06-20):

# Assembly Instructions
How to build your Handheld Ground Station kit

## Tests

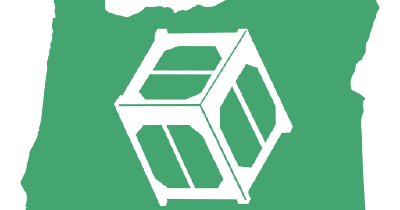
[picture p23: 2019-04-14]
software/rootfs/var/www/html/assets/img/test.png

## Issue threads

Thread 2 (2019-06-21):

Backplane PCB - back layer text needs to be mirrored

Chana030102, 2019-06-21:
When manufactured, all text on the back layer is flipped/mirrored and doesn't read correctly.  Can be fixed by changing the footprint and using the "mirror" option to flip it.

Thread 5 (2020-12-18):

GNU Radio -or- other decoder available?

K4KDR, 2020-12-18:
Hello!

Many Amateur Radio operators already have the ability to receive S-Band downlinks with existing antenna & SDR receivers.

As an alternative to your Rasp Pi Ground Station decoder for the reception of image & telemetry downlinks, is there a GNU Radio flowgraph or other software decoder available for those of us who can receive S-Band directly?

Thank you very much!

-Scott,  K4KDR

gusbunce, 2021-04-25:
Im happy to write a GNU Radio flowgraph for a decoder.

gusbunce, 2021-04-25:
Just created a branch will start work now.

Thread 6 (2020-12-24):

image length check failed

K4KDR, 2020-12-24:
Hello!

I have the Ground Station side working correctly on a Pi-3b and can access the embedded web server to view the "OreSat Live" page as it awaits an image.

However, after loading the "oresat-live-mini-oresat" image onto a camera-equipped Pi-zero, no image is successfully received.  Instead, the ground station logs a steady stream of:

```
Waiting for start-of-frame sync bytes...........
image length check failed 2356233934 != 2749031310
Waiting for start-of-frame sync bytes...........
image length check failed 3577411304 != 1079991195
Waiting for start-of-frame sync bytes...........
image length check failed 973807810 != 3461556171
Waiting for start-of-frame sync bytes...........
image length check failed 550339395 != 2029166624
```

.... and so forth.

Could you please advise whether the Ground-Station or "Mini" code can be adjusted so that the bytes received pass the length check so that the received image can be passed on & viewed in the web interface.

Thank you!

RussellSenior, 2021-01-02:
Hi @KDKDR, I started work on revisiting this last spring, but it's been stalled since covid. I set up a testbed and can send you my doc on what I did.

K4KDR, 2021-01-02:
That would be GREAT, Russell - thank you!

Please feel free to post links here or email me directly at scott23192@gmail.com

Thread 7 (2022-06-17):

KiCAD SMA footprint

davidalay, 2022-06-17:
The SMA connector on the HGS mainboard KiCAD port is broken. The one used in the PCB-Legos folder works

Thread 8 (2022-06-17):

Verify correct footprint of LNA on the HGS

davidalay, 2022-06-17:

Closed 2024-09-11.

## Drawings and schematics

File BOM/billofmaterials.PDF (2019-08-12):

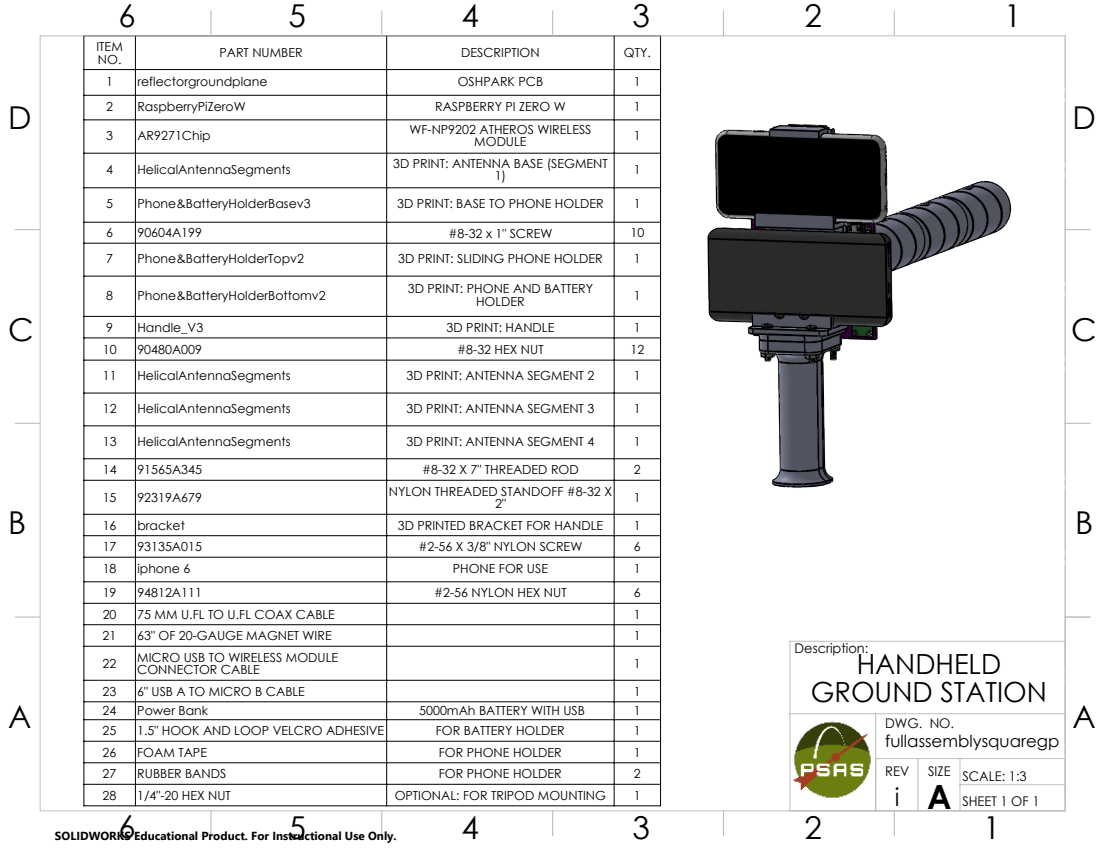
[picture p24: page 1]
1/4"-20 HEX NUT; OPTIONAL: FOR TRIPOD MOUNTING; REV; SCALE: 1:3; SHEET 1 OF 1; GROUND STATION

ITEM NO. | PART NUMBER | DESCRIPTION | QTY.

1 | reflectorgroundplane | OSHPARK PCB | 1
2 | RaspberryPiZeroW | RASPBERRY PI ZERO W | 1
3 | AR9271Chip | WF-NP9202 ATHEROS WIRELESS MODULE | 1

4 | HelicalAntennaSegments | 3D PRINT: ANTENNA BASE (SEGMENT 1) 1

5 | Phone&BatteryHolderBasev3 | 3D PRINT: BASE TO PHONE HOLDER | 1
6 | 90604A199 | #8-32 x 1" SCREW | 10
7 | Phone&BatteryHolderTopv2 | 3D PRINT: SLIDING PHONE HOLDER | 1
8 | Phone&BatteryHolderBottomv2 | 3D PRINT: PHONE AND BATTERY HOLDER | 1

9 | Handle_V3 | 3D PRINT: HANDLE | 1
10 | 90480A009 | #8-32 HEX NUT | 12
11 | HelicalAntennaSegments | 3D PRINT: ANTENNA SEGMENT 2 | 1
12 | HelicalAntennaSegments | 3D PRINT: ANTENNA SEGMENT 3 | 1
13 | HelicalAntennaSegments | 3D PRINT: ANTENNA SEGMENT 4 | 1
14 | 91565A345 | #8-32 X 7" THREADED ROD | 2
15 | 92319A679 | NYLON THREADED STANDOFF #8-32 X 2" | 1

16 | bracket | 3D PRINTED BRACKET FOR HANDLE | 1
17 | 93135A015 | #2-56 X 3/8" NYLON SCREW | 6
18 | iphone 6 | PHONE FOR USE | 1
19 | 94812A111 | #2-56 NYLON HEX NUT | 6
20 | 75 MM U.FL TO U.FL COAX CABLE | | 1
21 | 63" OF 20-GAUGE MAGNET WIRE | | 1
22 | MICRO USB TO WIRELESS MODULE CONNECTOR CABLE | | 1

23 | 6" USB A TO MICRO B CABLE | | 1
24 | Power Bank | 5000mAh BATTERY WITH USB | 1
25 | 1.5" HOOK AND LOOP VELCRO ADHESIVE | FOR BATTERY HOLDER | 1
26 | FOAM TAPE | FOR PHONE HOLDER | 1
27 | RUBBER BANDS | FOR PHONE HOLDER | 2

DWG. NO. fullassemblysquaregp

SOLIDWORKS Educational Product. For Instructional Use Only.

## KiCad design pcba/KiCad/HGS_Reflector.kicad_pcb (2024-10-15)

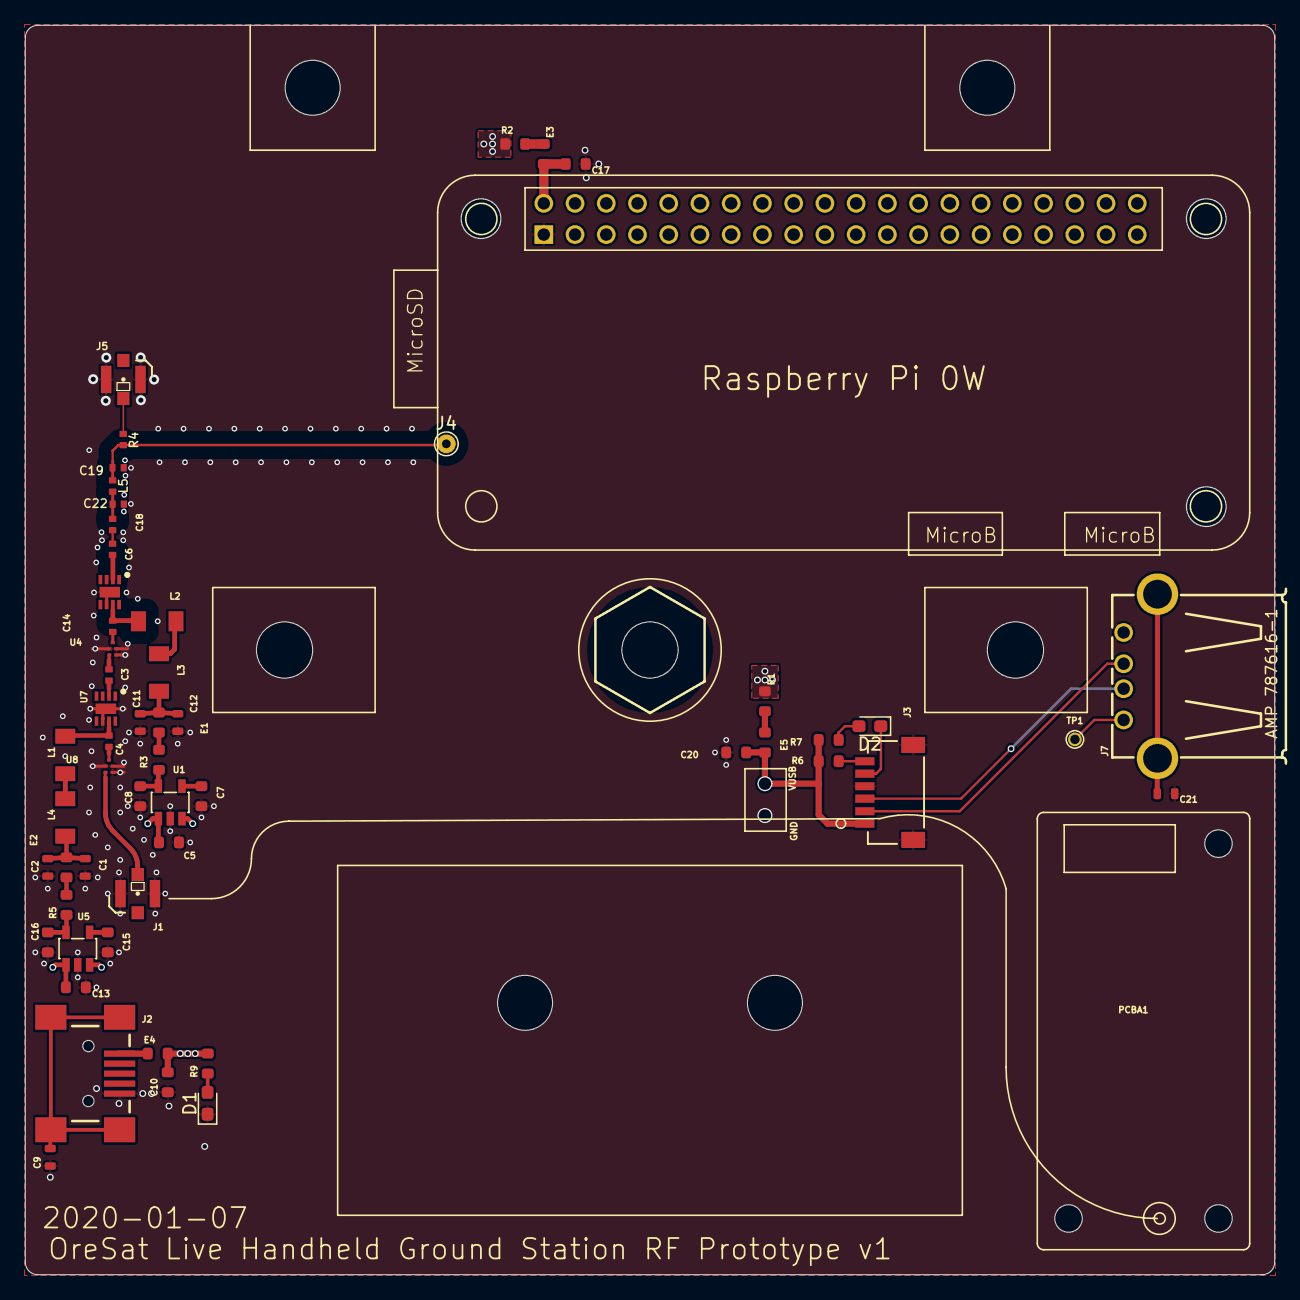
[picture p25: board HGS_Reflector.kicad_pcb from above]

Board: 4 copper layers, 100.0 x 100.0 mm, 64 parts (0 on the bottom side), 38 nets.

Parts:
@HOLE0, @HOLE1, @HOLE2, @HOLE3, @HOLE4, @HOLE5, @HOLE6: (no value)
C1, C9, C11, C21: 100 pF; 0603-C-NOSILK
C2, C12: 1 uF; 0603-C-NOSILK
C3, C4, C6, C14, C18: 100 pF; 0402-C-NOSILK
C5, C10, C13, C17, C20: 1 uF; 0603-B-NOSILK
C7, C15: 10 nF; 0603-B-NOSILK
C8, C16: 2.2 uF; 0603-B-NOSILK
C19: 0.9 pF; 0402-C-NOSILK
C22: 1.0 pF; 0402-C-NOSILK
D1, D2: Green; LED_0603_1608Metric_Pad1.05x0.95mm_HandSolder
E1, E2, E5: BLM18GG471SZ1D; 0603-B-NOSILK
E3, E4: BLM18DN381SZ1D; 0603-B-NOSILK
J1: U.FL
J2: USB_C_Plug_USB2.0; USB-MINIB
J3: SM06B-SRSS-TB(LF)(SN); CONN_SM06B-SRSS-TB_JST
J4: Conn_01x01_Pin; TestPoint_THTPad_D1.5mm_Drill0.7mm
J5: 132134-10; U.FL
J7: USB_HOST_W/CHASSIS_GND; GHI2_USB_HOST_HORIZONTAL_W_CHASSIS_GND
L1, L2: 10n; L3216C
L3, L4: 8n; L3216C
L5: 4.3 nH; 0402-C-NOSILK
PCBA1: WF-NP9202WF; WF-NP9202
PCBA2: RASP_PI_0WPI_0W; RASP_PI_0W
R1, R2, R3, R5, R6: 0; 0603-B-NOSILK
R4: R_Small_US; 0402-C-NOSILK
R7, R9: 1k; 0603-B-NOSILK
TP1: Test-Point; TestPoint-0.75mm-th
U1, U5: LP2985-N; SOT-23 LP2985
U2, U7: TQP3M9037
U4: QPQ1907
U8: B39162B9417K610; QPQ1907

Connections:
/RF1: C19.2, J4.1, L5.1, R4.2
/RF2: C18.2, C22.1, L5.2
/RF3: C6.2, U2.2 (RF_IN)
/RF4: C14.1, L2.1, U2.7 (RF_OUT)
GND: C1.2, C2.2, C5.1, C7.2, C8.2, C9.1, C10.1, C11.2, C12.2, C13.1, C15.2, C16.2, C17.1, C19.1, C20.1, C21.1, C22.2, D1.1 (K), J1.1 (GND@0), J1.2 (GND@1), J2.A1 (GND), J3.4, J3.7, J3.8 (7), J5.1 (GND@0), J5.2 (GND@1), J7.4 (GND), PCBA2.GND, U1.2 (GND), U2.6 (SHUT_DOWN), U2.9 (GND), U4.2 (GND), U4.3 (GND), U4.5 (GND), U5.2 (GND), U7.6 (SHUT_DOWN), U7.9 (GND), U8.2 (GND), U8.3 (GND), U8.5 (GND)
unnamed: C1.1, C2.1, E2.2, L4.2
unnamed: C11.1, C12.1, E1.2, L3.2
unnamed: C17.2, E3.2, PCBA2.5V
unnamed: C6.1, C18.1
unnamed: C20.2, E5.2, J3.1, R6.1, R7.2
unnamed: D1.2 (A), R9.1
unnamed: D2.2 (A), R7.1
unnamed: D2.1 (K), J3.5
unnamed: E1.1, R3.2
unnamed: E2.1, R5.2
unnamed: E3.1, R2.2
unnamed: E4.1, J2.A4 (VBUS)
unnamed: E5.1, R1.2
unnamed: J1.FEED (SIGNAL), U8.4 (OUT)
unnamed: C9.2, J2.S1 (SHIELD)
unnamed: J3.6, R6.2
unnamed: J5.FEED (SIGNAL), R4.1
unnamed: C21.2, J7.5 (CG1), J7.6 (CG2)
unnamed: J3.2, J7.3 (D+)
unnamed: J3.3, J7.2 (D-)
unnamed: J7.1 (VBUS), TP1.1
unnamed: L1.2, L4.1
unnamed: L2.2, L3.1
unnamed: C7.1, U1.4 (BYPASS)
unnamed: C8.1, R3.1, U1.5 (VOUT)
unnamed: C14.2, U4.1 (IN)
unnamed: C3.1, U4.4 (OUT)
unnamed: C15.1, U5.4 (BYPASS)
unnamed: C16.1, R5.1, U5.5 (VOUT)
unnamed: C3.2, U7.2 (RF_IN)
unnamed: C4.1, L1.1, U7.7 (RF_OUT)
unnamed: C4.2, U8.1 (IN)
VBUS: C5.2, C10.2, C13.2, E4.2, R1.1, R2.1, R9.2, U1.1 (VIN), U1.3 (EN), U5.1 (VIN), U5.3 (EN)

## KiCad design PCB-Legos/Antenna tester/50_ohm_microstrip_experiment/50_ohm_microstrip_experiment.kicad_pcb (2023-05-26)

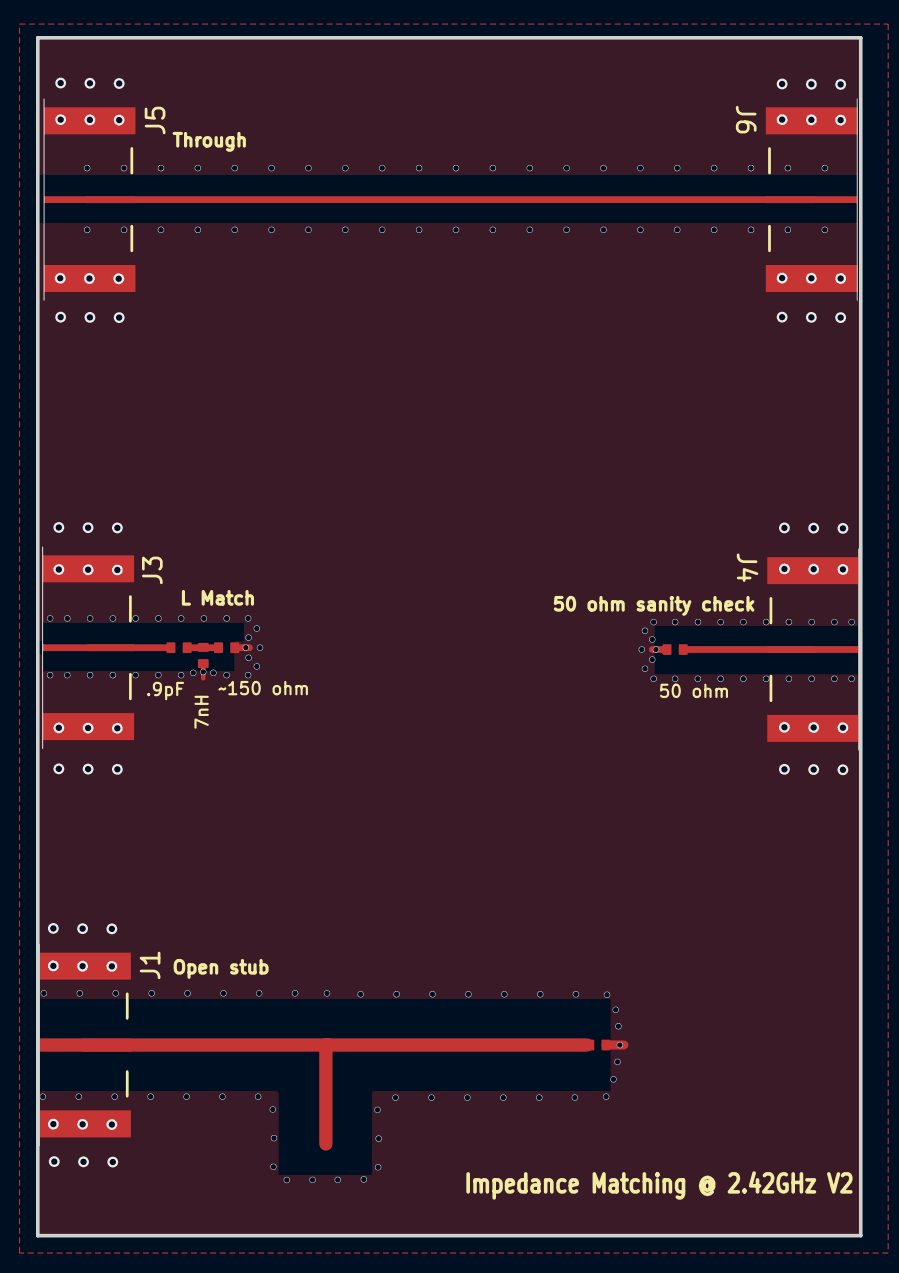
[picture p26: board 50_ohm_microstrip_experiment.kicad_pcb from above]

Board: 4 copper layers, 45.7 x 66.5 mm, 10 parts (0 on the bottom side), 5 nets.

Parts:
C1: .9pF; .0402-C-NOSILK
J1, J3, J4, J5, J6: Conn_Coaxial; CONN_142-0701-851_CIN
L1: 7nH; .0402-C-NOSILK
R1: 50; .0402-C-NOSILK
R5: ~150 ohm; .0402-C-NOSILK
R6: 50 ohm; .0402-C-NOSILK

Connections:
GND: J1.2 (Ext), J1.3, J1.4, J1.5, J3.2 (Ext), J3.3, J3.4, J3.5, J4.2 (Ext), J4.3, J4.4, J4.5, J5.2 (Ext), J5.3, J5.4, J6.2 (Ext), J6.3, J6.5, L1.2, R1.1, R5.1, R6.1
unnamed: J1.1 (In), R1.2
unnamed: C1.2, J3.1 (In), J4.1 (In)
unnamed: J5.1 (In), J6.1 (In)
unnamed: C1.1, L1.1, R5.2, R6.2

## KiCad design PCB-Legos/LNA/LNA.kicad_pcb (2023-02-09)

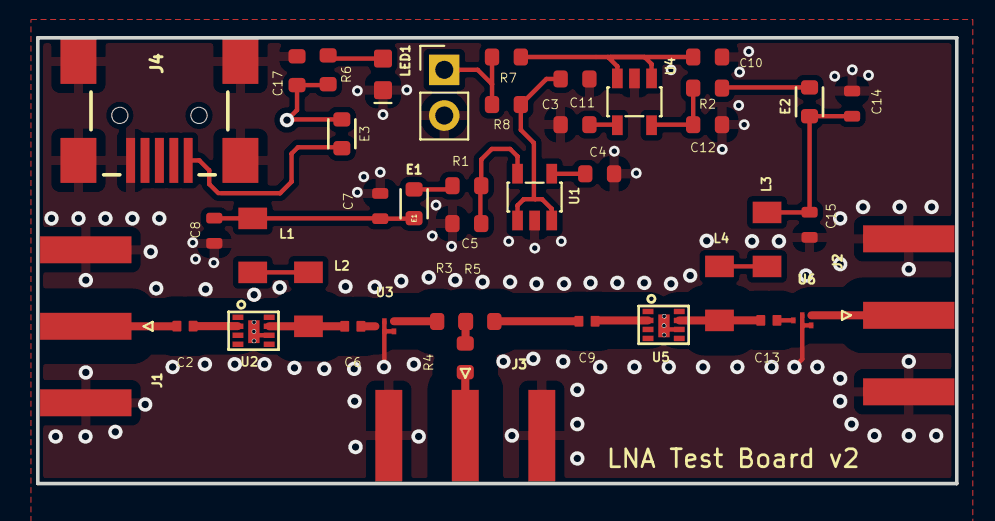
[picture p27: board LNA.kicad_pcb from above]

Board: 4 copper layers, 51.1 x 24.8 mm, 42 parts (0 on the bottom side), 26 nets.

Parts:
C2, C6, C9, C13: 100 pF; .0402-C-NOSILK
C3, C10, C17: 1 uF; .0603-B-NOSILK
C4, C11: 10 nF; .0603-B-NOSILK
C5, C12: 2.2 uF; .0603-B-NOSILK
C7, C14: 100 pF; .0603-C-NOSILK
C8, C15: 1 uF; .0603-C-NOSILK
E1, E2: BLM18GG471SZ1D; .0603-B
E3: BLM18DN381SZ1D; .0603-B
H2: VUSB; PinHeader_1x02_P2.54mm_Vertical
J1, J2, J3: Conn_Coaxial; SMA_Amphenol_132289_EdgeMount
J4: 474-PRT-00587; USB-MINIB
L1, L3: 8 nH; L3216C
L2, L4: 10 nH; L3216C
LED1: GREEN; LED-0603
R1, R2, R3, R4, R5, R7, R8: 0; .0603-B-NOSILK
R6: 1k; .0603-B-NOSILK
U1, U4: LP2985XX-N; SOT-23
U2, U5: LNA-TP3M9037; TP3M9037
U3, U6: QPQ1907

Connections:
GND: C3.1, C4.2, C5.2, C7.2, C8.2, C10.1, C11.2, C12.2, C14.2, C15.2, C17.1, H2.2, J1.2 (Ext), J2.2 (Ext), J3.2 (Ext), J4.GND, J4.S1 (SHIELD), J4.S2 (SHIELD), J4.S3 (SHIELD), J4.S4 (SHIELD), LED1.C, U1.2 (GND), U3.GND, U3.GND2 (GND), U3.GND3 (GND), U4.2 (GND), U6.GND, U6.GND2 (GND), U6.GND3 (GND)
unnamed: C2.1, J1.1 (In)
unnamed: C3.2, R8.1, U1.1 (VIN), U1.3 (EN)
unnamed: C4.1, U1.4 (BYPASS)
unnamed: C5.1, R1.1, U1.5 (VOUT)
unnamed: C6.1, L2.1
unnamed: C6.2, U3.INPUT (RF_IN)
unnamed: C7.1, C8.1, E1.2, L1.2
unnamed: C9.1, R5.2
unnamed: C10.2, R7.1, U4.1 (VIN), U4.3 (EN)
unnamed: C11.1, U4.4 (BYPASS)
unnamed: C12.1, R2.1, U4.5 (VOUT)
unnamed: C13.1, L4.1
unnamed: C13.2, U6.INPUT (RF_IN)
unnamed: C14.1, C15.1, E2.2, L3.2
unnamed: E1.1, R1.2
unnamed: E2.1, R2.2
unnamed: E3.1, J4.VBUS
unnamed: J2.1 (In), U6.OUTPUT (RF-OUT)
unnamed: J3.1 (In), R4.2
unnamed: L1.1, L2.2
unnamed: L3.1, L4.2
unnamed: LED1.A, R6.1
unnamed: R3.1, U3.OUTPUT (RF-OUT)
unnamed: R3.2, R4.1, R5.1
VUSB: C17.2, E3.2, H2.1, R6.2, R7.2, R8.2

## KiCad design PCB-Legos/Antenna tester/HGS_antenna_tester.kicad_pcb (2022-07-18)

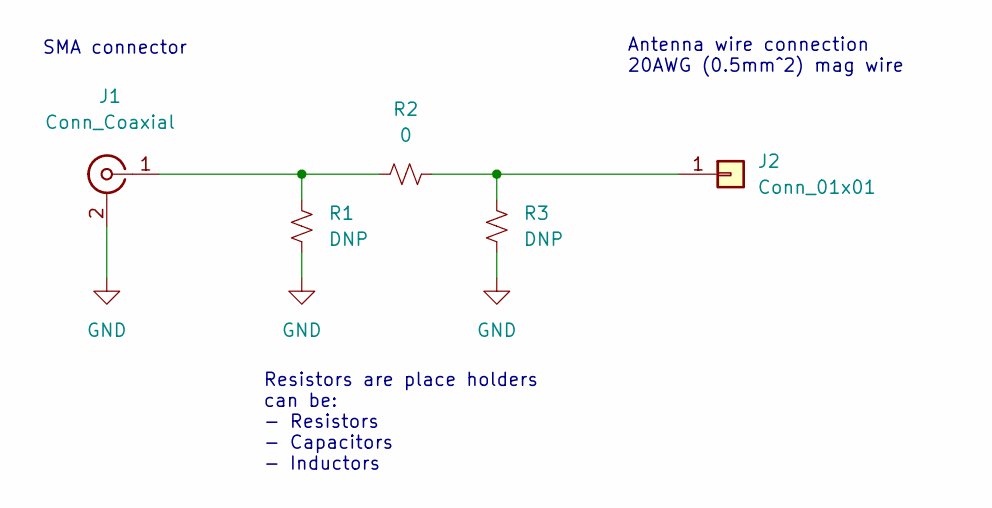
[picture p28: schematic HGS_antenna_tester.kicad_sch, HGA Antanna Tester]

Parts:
J1: Conn_Coaxial; SMA_Amphenol_132134-10_Vertical
J2: Conn_01x01; SolderWire-0.5sqmm_1x01_D0.9mm_OD2.1mm
R1, R3: DNP; R_0402_1005Metric_Pad0.72x0.64mm_HandSolder
R2: 0; R_0402_1005Metric_Pad0.72x0.64mm_HandSolder

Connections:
GND: J1.2 (Ext), R1.2, R3.2
unnamed: J1.1 (In), R1.1, R2.1
unnamed: J2.1, R2.2, R3.1

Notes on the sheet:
Antenna wire connection 20AWG (0.5mm^2) mag wire
SMA connector
Resistors are place holders can be: - Resistors - Capacitors - Inductors

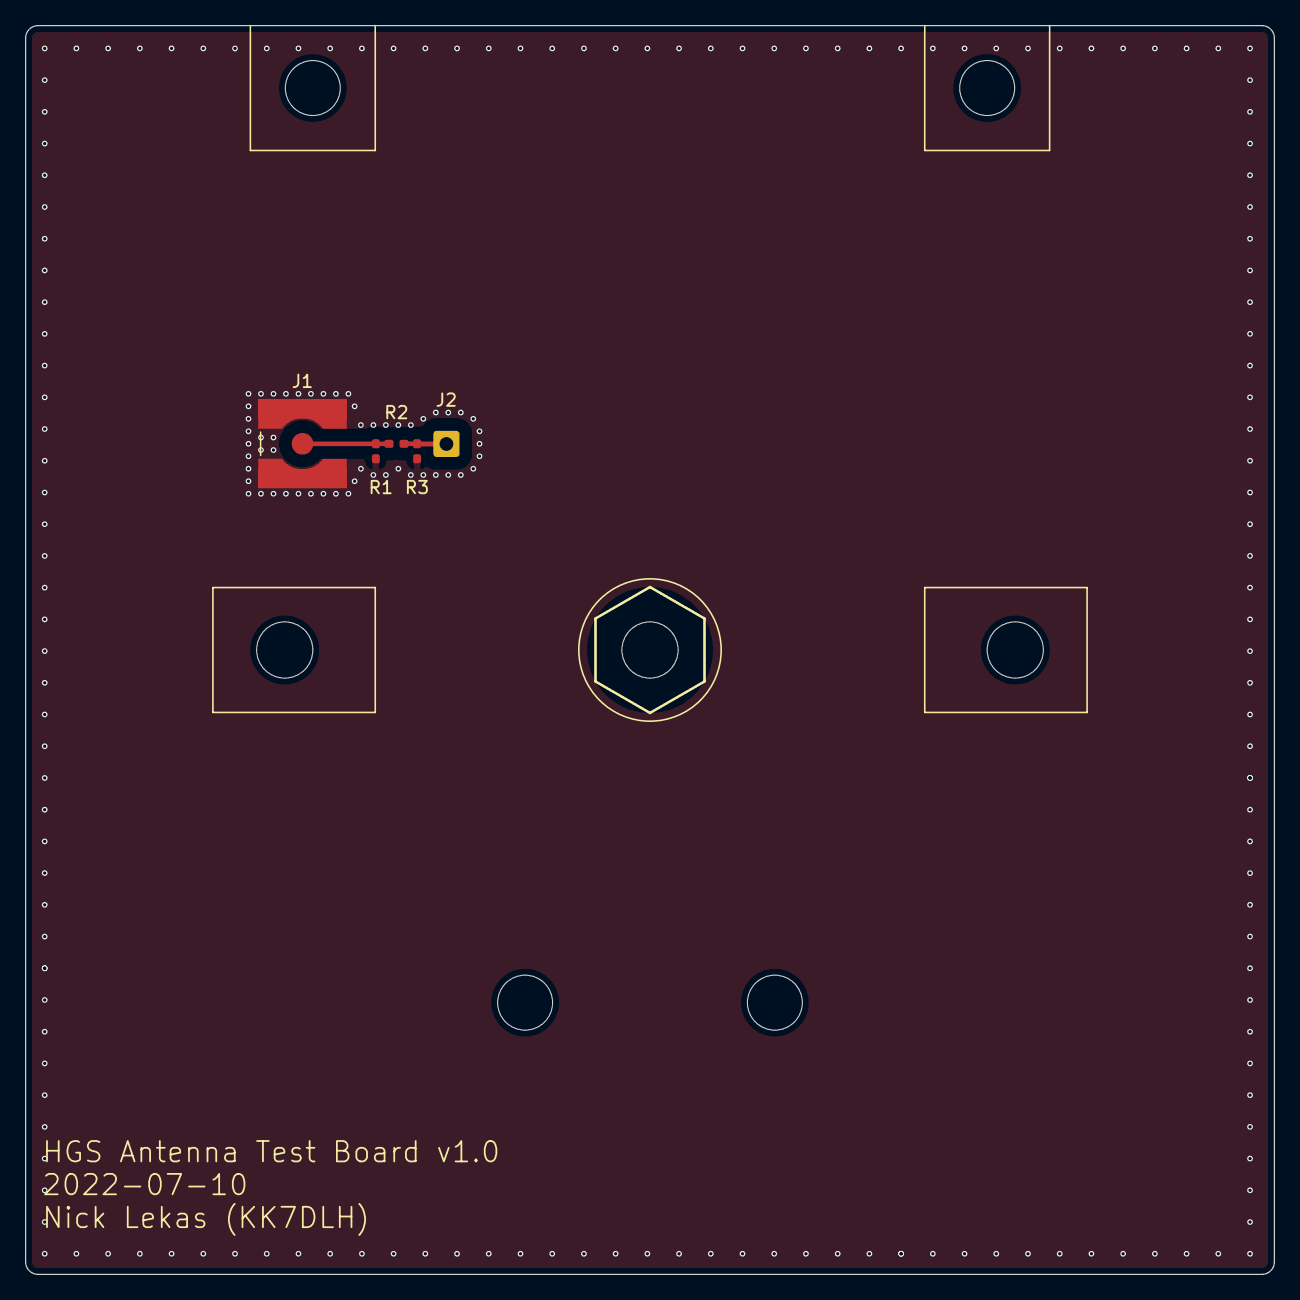
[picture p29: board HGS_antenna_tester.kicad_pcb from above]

Board: 4 copper layers, 100.0 x 100.0 mm, 12 parts (0 on the bottom side), 3 nets.

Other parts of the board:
@HOLE0, @HOLE1, @HOLE2, @HOLE3, @HOLE4, @HOLE5, @HOLE6: (no value)

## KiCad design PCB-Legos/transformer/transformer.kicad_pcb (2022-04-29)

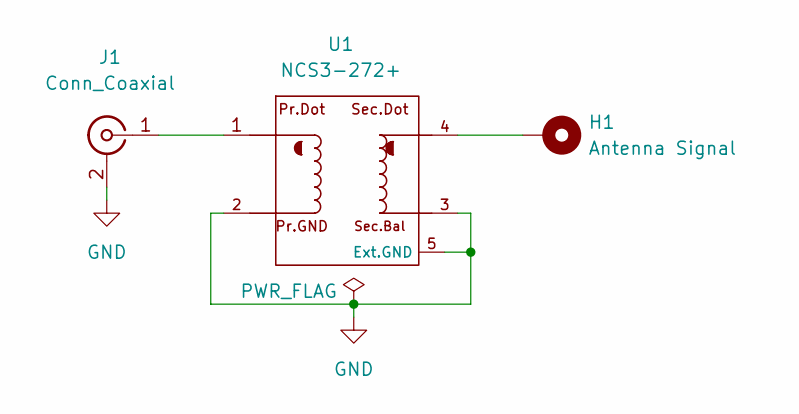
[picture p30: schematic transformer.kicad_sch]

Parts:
H1: Antenna Signal; Pin_D0.7mm_L6.5mm_W1.8mm_FlatFork
J1: Conn_Coaxial; J-Amphenol-132134-10-SMA-F-SMT-vertical
U1: NCS3-272+; U-Minicircuits-GE0805C-9

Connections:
GND: J1.2 (Ext), U1.2, U1.3, U1.5 (Ext.GND)
unnamed: H1.1, U1.4
unnamed: J1.1 (In), U1.1

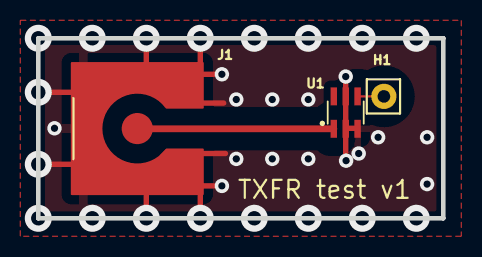
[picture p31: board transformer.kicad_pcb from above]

Board: 4 copper layers, 22.5 x 10.0 mm, 3 parts (0 on the bottom side), 3 nets.

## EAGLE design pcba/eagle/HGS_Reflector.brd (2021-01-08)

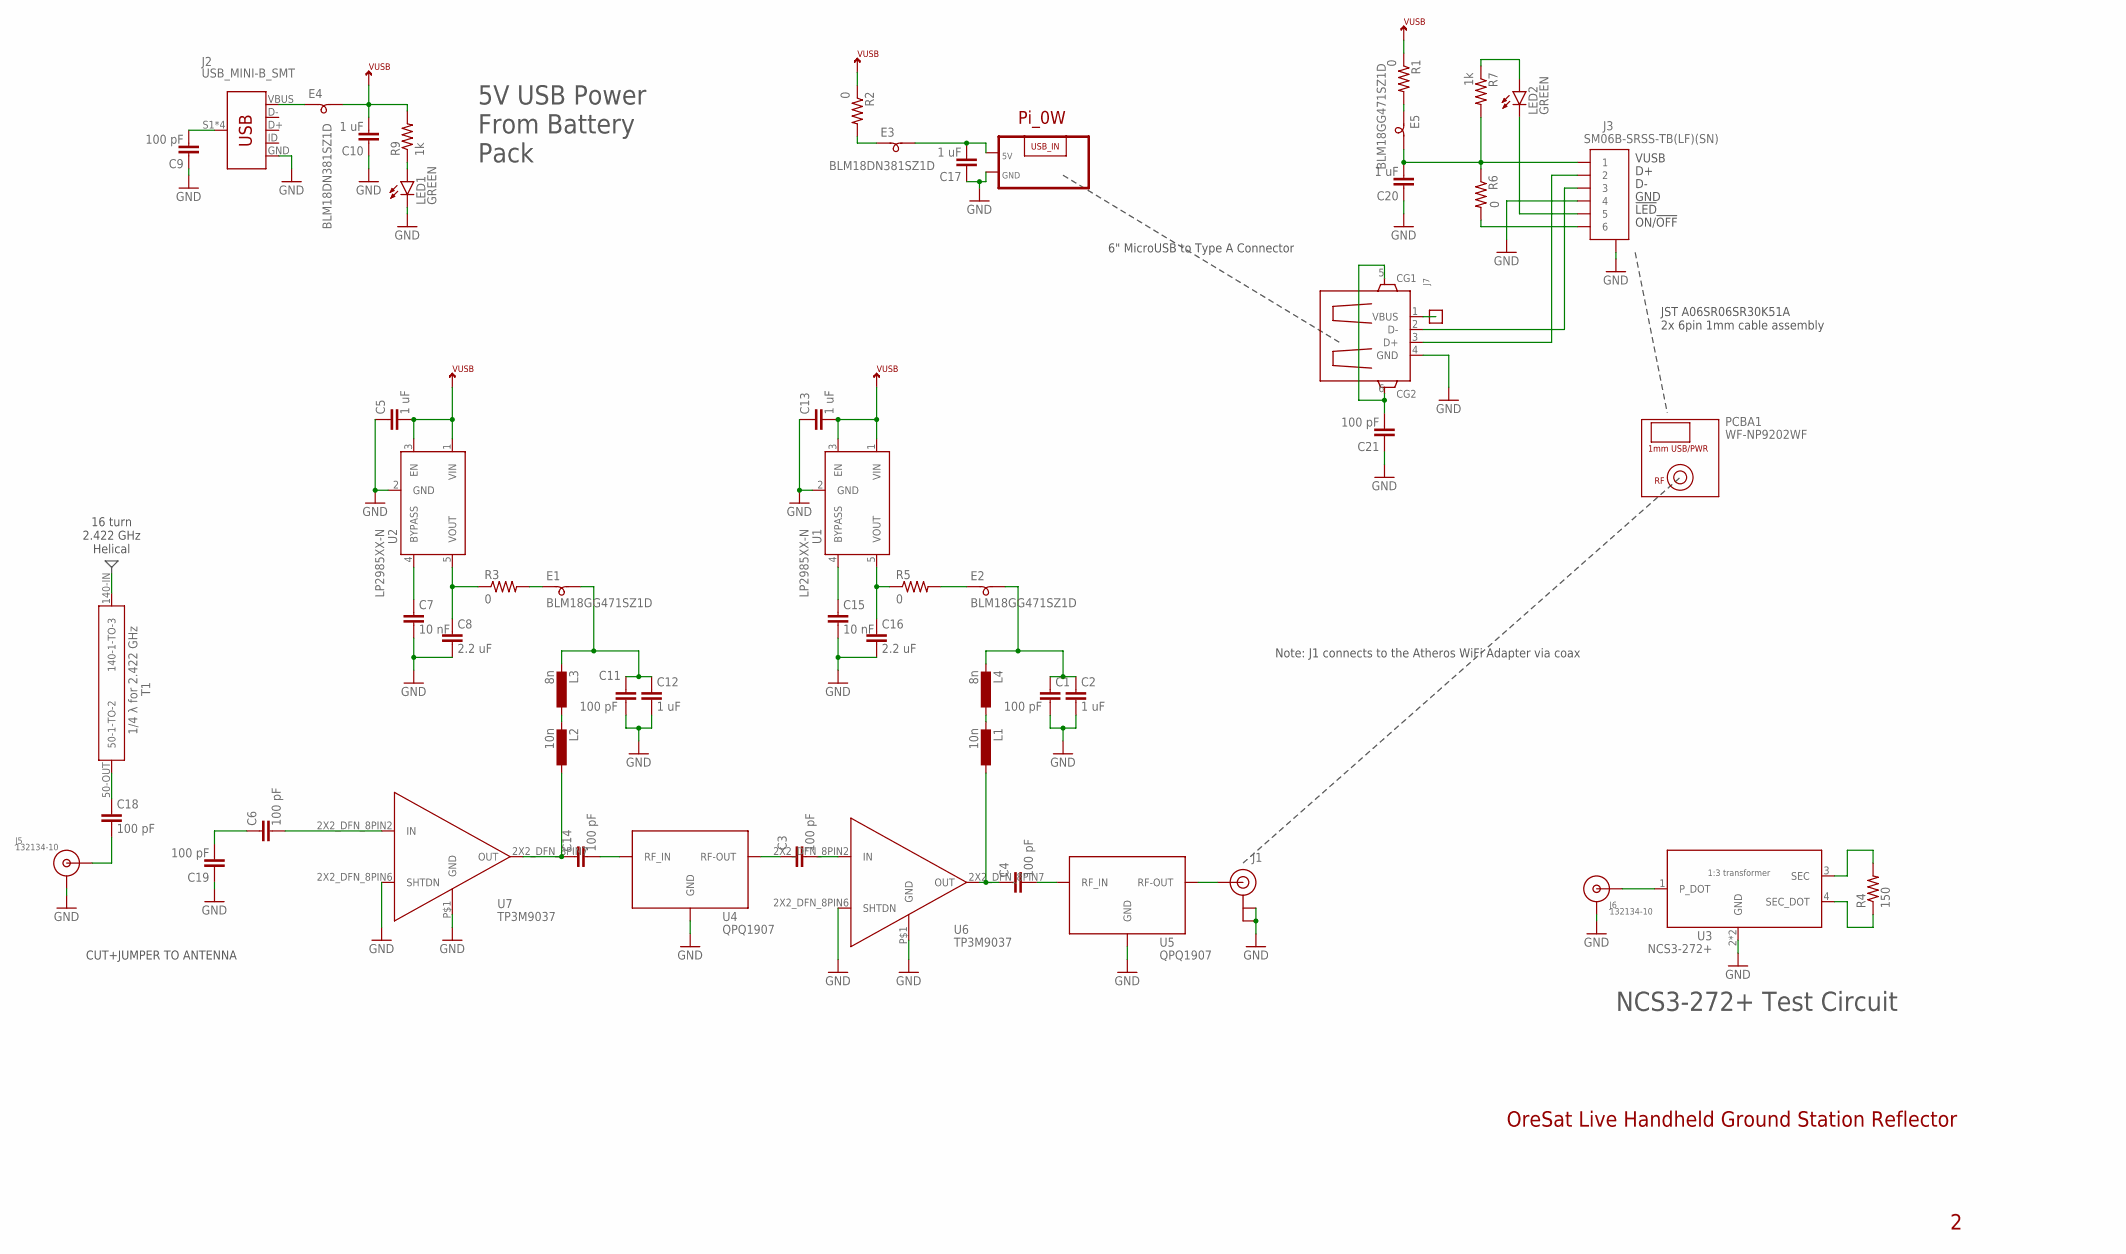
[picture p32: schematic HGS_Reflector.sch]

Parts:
C1, C9, C11, C21: 100 pF; .0603-C-NOSILK
C2, C12: 1 uF; .0603-C-NOSILK
C3, C4, C6, C14, C18, C19: 100 pF; .0402-C-NOSILK
C5, C10, C13, C17, C20: 1 uF; .0603-B-NOSILK
C7, C15: 10 nF; .0603-B-NOSILK
C8, C16: 2.2 uF; .0603-B-NOSILK
E1, E2, E5: BLM18GG471SZ1D; .0603-B
E3, E4: BLM18DN381SZ1D; .0603-B
J1: U.FL
J2: USB_MINI-B_SMT; USB-MINIB
J3: SM06B-SRSS-TB(LF)(SN); CONN_SM06B-SRSS-TB_JST
J5, J6: 132134-10
J7: USB_HOST_W/CHASSIS_GND; GHI2_USB_HOST_HORIZONTAL_W/CHASSIS_GND
L1, L2: 10n; L3216C
L3, L4: 8n; L3216C
LED1, LED2: GREEN; LED-0603
PCBA1: WF-NP9202WF; WF-NP9202
PCBA2: RASP_PI_0WPI_0W; RASP_PI_0W
R1, R2, R3, R5, R6: 0; .0603-B-NOSILK
R4: 150; .0402-C-NOSILK
R7, R9: 1k; .0603-B-NOSILK
T1: QWT2.4222; QWT_2.422G-V2
TP2: TEST-POINT-LARGE-SQUARE; 1X01
U1, U2: LP2985XX-N; SOT-23
U3: NCS3-272+; GE0805C-1
U4, U5: QPQ1907
U6, U7: LNA-TP3M9037; TP3M9037

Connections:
GND: C1.2, C2.2, C5.1, C7.2, C8.2, C9.1, C10.1, C11.2, C12.2, C13.1, C15.2, C16.2, C17.1, C19.1, C20.1, C21.1, J1.1 (GND), J1.2 (GND), J2.GND, J3.4, J3.7, J3.8 (7), J5.SHIELD (GND), J6.SHIELD (GND), J7.4 (GND), LED1.C, PCBA2.GND, U1.2 (GND), U2.2 (GND), U3.2 (GND), U3.5 (GND), U4.GND, U4.GND2 (GND), U4.GND3 (GND), U5.GND, U5.GND2 (GND), U5.GND3 (GND), U6.2X2_DFN_8PIN6 (SHTDN), U6.P$1 (GND), U7.2X2_DFN_8PIN6 (SHTDN), U7.P$1 (GND)
HELICAL: T1.140-IN (140-1-TO-3)
unnamed: C7.1, U2.4 (BYPASS)
unnamed: E1.1, R3.2
unnamed: C4.2, U5.INPUT (RF_IN)
unnamed: C3.1, U4.OUTPUT (RF-OUT)
unnamed: J1.FEED (SIGNAL), U5.OUTPUT (RF-OUT)
unnamed: C14.2, U4.INPUT (RF_IN)
unnamed: L2.2, L3.1
unnamed: C3.2, U6.2X2_DFN_8PIN2 (IN)
unnamed: E2.1, R5.2
unnamed: LED1.A, R9.1
unnamed: C6.2, U7.2X2_DFN_8PIN2 (IN)
unnamed: C9.2, J2.S1 (SHIELD), J2.S2 (SHIELD), J2.S3 (SHIELD), J2.S4 (SHIELD)
unnamed: C4.1, L1.1, U6.2X2_DFN_8PIN7 (OUT)
unnamed: L1.2, L4.1
unnamed: C17.2, E3.2, PCBA2.5V
unnamed: C14.1, L2.1, U7.2X2_DFN_8PIN7 (OUT)
unnamed: E4.1, J2.VBUS
unnamed: E3.1, R2.2
unnamed: C15.1, U1.4 (BYPASS)
unnamed: C11.1, C12.1, E1.2, L3.2
unnamed: C1.1, C2.1, E2.2, L4.2
unnamed: C16.1, R5.1, U1.5 (VOUT)
unnamed: C18.2, J5.CENTER (SIG)
unnamed: J6.CENTER (SIG), U3.1 (P_DOT)
unnamed: C8.1, R3.1, U2.5 (VOUT)
unnamed: R4.2, U3.3 (SEC)
unnamed: R4.1, U3.4 (SEC_DOT)
unnamed: C6.1, C19.2
unnamed: C20.2, E5.2, J3.1, R6.1, R7.2
unnamed: E5.1, R1.2
unnamed: J3.6, R6.2
unnamed: LED2.A, R7.1
unnamed: J3.2, J7.3 (D+)
unnamed: J3.5, LED2.C
unnamed: J3.3, J7.2 (D-)
unnamed: J7.1 (VBUS), TP2.1
unnamed: C21.2, J7.5 (CG1), J7.6 (CG2)
T1-50: C18.1, T1.50-OUT (50-1-TO-2)
VUSB: C5.2, C10.2, C13.2, E4.2, R1.1, R2.1, R9.2, U1.1 (VIN), U1.3 (EN), U2.1 (VIN), U2.3 (EN)

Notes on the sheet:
OreSat Live Handheld Ground Station Reflector
Note: J1 connects to the Atheros WiFi Adapter via coax
16 turn 2.422 GHz Helical
NCS3-272+ Test Circuit
5V USB Power From Battery Pack
CUT+JUMPER TO ANTENNA
VUSB
GND
!LED
ON/!OFF
JST A06SR06SR30K51A 2x 6pin 1mm cable assembly
6" MicroUSB to Type A Connector

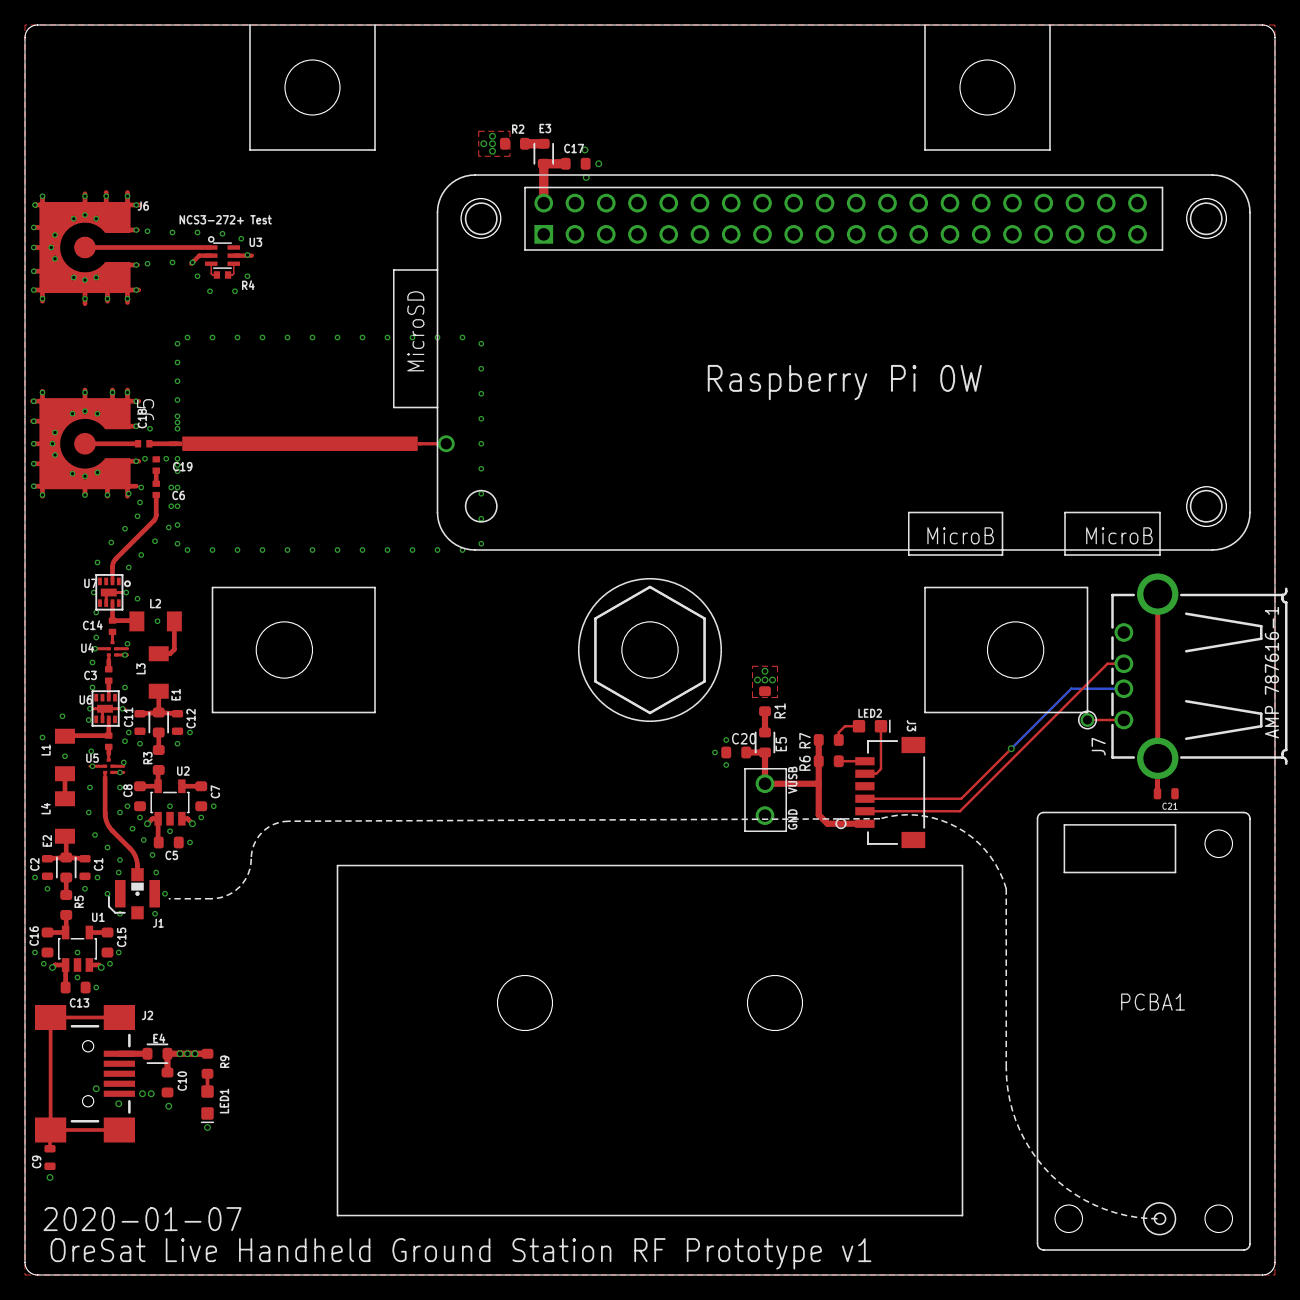
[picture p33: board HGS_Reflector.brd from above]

Board: 4 copper layers, 100.0 x 100.0 mm, 57 parts (0 on the bottom side), 40 nets.

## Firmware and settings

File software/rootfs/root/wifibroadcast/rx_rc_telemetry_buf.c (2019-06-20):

// rx_rc_telemetry_buf by Rodizio. Based on wifibroadcast rx by Befinitiv. Mavlink code contributed by dino_de. Licensed under GPL2
// Dirty buffering implementation to cope with out-of-order reception of telemetry packets with multiple RX adapters.
// Will be integrated into rx_rc_telemetry in the future hopefully.
// If you have some C coding skills, a proper buffering implementation would be appreciated ;)
/*
 *   This program is free software; you can redistribute it and/or modify
 *   it under the terms of the GNU General Public License as published by
 *   the Free Software Foundation; version 2.
 *
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
 *   You should have received a copy of the GNU General Public License along
 *   with this program; if not, write to the Free Software Foundation, Inc.,
 *   51 Franklin Street, Fifth Floor, Boston, MA 02110-1301 USA.
 */

#include "lib.h"
#include "wifibroadcast.h"
#include "radiotap.h"
#include <time.h>
#include <sys/resource.h>
#include <fcntl.h>        // serialport
#include <termios.h>      // serialport
#include "mavlink/common/mavlink.h"

// this is where we store a summary of the information from the radiotap header
typedef struct {
	int m_nChannel;
	int m_nChannelFlags;
	int m_nRate;
	int m_nAntenna;
	int m_nRadiotapFlags;
} __attribute__((packed)) PENUMBRA_RADIOTAP_DATA;


typedef struct {
	uint32_t seq;
	uint16_t len;
	uint8_t filled;
	char payload[400];
} buffer_t;
buffer_t buffer[100];


//uint32_t seqbuffer[5];

int flagHelp = 0;
int param_baudrate = 0;
int param_rc_protocol = 0;
int param_output = 0;
int param_port = 0;
int param_debug = 0;
char *param_serialport = "none";

uint32_t seqno_telemetry = 0;
uint8_t seqno_rc = 0;
uint32_t seqnolast_telemetry = 0;
uint8_t seqnolast_rc = 0;

int seqnumplayed = 0;

int telemetry_received_yet = 0;
int rc_received_yet = 0;


int port_encoded;

wifibroadcast_rx_status_t *rx_status = NULL;
wifibroadcast_rx_status_t *rx_status_rc = NULL;

uint16_t sumdcrc = 0;
uint16_t ibuschecksum = 0;


int lastseq;

const uint16_t sumdcrc16_table[256] = {
    0x0000, 0x1021, 0x2042, 0x3063, 0x4084, 0x50A5, 0x60C6, 0x70E7, 0x8108, 0x9129, 0xA14A, 0xB16B, 0xC18C, 0xD1AD, 0xE1CE, 0xF1EF,
    0x1231, 0x0210, 0x3273, 0x2252, 0x52B5, 0x4294, 0x72F7, 0x62D6, 0x9339, 0x8318, 0xB37B, 0xA35A, 0xD3BD, 0xC39C, 0xF3FF, 0xE3DE,
    0x2462, 0x3443, 0x0420, 0x1401, 0x64E6, 0x74C7, 0x44A4, 0x5485, 0xA56A, 0xB54B, 0x8528, 0x9509, 0xE5EE, 0xF5CF, 0xC5AC, 0xD58D,
    0x3653, 0x2672, 0x1611, 0x0630, 0x76D7, 0x66F6, 0x5695, 0x46B4, 0xB75B, 0xA77A, 0x9719, 0x8738, 0xF7DF, 0xE7FE, 0xD79D, 0xC7BC,
    0x48C4, 0x58E5, 0x6886, 0x78A7, 0x0840, 0x1861, 0x2802, 0x3823, 0xC9CC, 0xD9ED, 0xE98E, 0xF9AF, 0x8948, 0x9969, 0xA90A, 0xB92B,
    0x5AF5, 0x4AD4, 0x7AB7, 0x6A96, 0x1A71, 0x0A50, 0x3A33, 0x2A12, 0xDBFD, 0xCBDC, 0xFBBF, 0xEB9E, 0x9B79, 0x8B58, 0xBB3B, 0xAB1A,
    0x6CA6, 0x7C87, 0x4CE4, 0x5CC5, 0x2C22, 0x3C03, 0x0C60, 0x1C41, 0xEDAE, 0xFD8F, 0xCDEC, 0xDDCD, 0xAD2A, 0xBD0B, 0x8D68, 0x9D49,
    0x7E97, 0x6EB6, 0x5ED5, 0x4EF4, 0x3E13, 0x2E32, 0x1E51, 0x0E70, 0xFF9F, 0xEFBE, 0xDFDD, 0xCFFC, 0xBF1B, 0xAF3A, 0x9F59, 0x8F78,
    0x9188, 0x81A9, 0xB1CA, 0xA1EB, 0xD10C, 0xC12D, 0xF14E, 0xE16F, 0x1080, 0x00A1, 0x30C2, 0x20E3, 0x5004, 0x4025, 0x7046, 0x6067,
    0x83B9, 0x9398, 0xA3FB, 0xB3DA, 0xC33D, 0xD31C, 0xE37F, 0xF35E, 0x02B1, 0x1290, 0x22F3, 0x32D2, 0x4235, 0x5214, 0x6277, 0x7256,
    0xB5EA, 0xA5CB, 0x95A8, 0x8589, 0xF56E, 0xE54F, 0xD52C, 0xC50D, 0x34E2, 0x24C3, 0x14A0, 0x0481, 0x7466, 0x6447, 0x5424, 0x4405,
    0xA7DB, 0xB7FA, 0x8799, 0x97B8, 0xE75F, 0xF77E, 0xC71D, 0xD73C, 0x26D3, 0x36F2, 0x0691, 0x16B0, 0x6657, 0x7676, 0x4615, 0x5634,
    0xD94C, 0xC96D, 0xF90E, 0xE92F, 0x99C8, 0x89E9, 0xB98A, 0xA9AB, 0x5844, 0x4865, 0x7806, 0x6827, 0x18C0, 0x08E1, 0x3882, 0x28A3,
    0xCB7D, 0xDB5C, 0xEB3F, 0xFB1E, 0x8BF9, 0x9BD8, 0xABBB, 0xBB9A, 0x4A75, 0x5A54, 0x6A37, 0x7A16, 0x0AF1, 0x1AD0, 0x2AB3, 0x3A92,
    0xFD2E, 0xED0F, 0xDD6C, 0xCD4D, 0xBDAA, 0xAD8B, 0x9DE8, 0x8DC9, 0x7C26, 0x6C07, 0x5C64, 0x4C45, 0x3CA2, 0x2C83, 0x1CE0, 0x0CC1,
    0xEF1F, 0xFF3E, 0xCF5D, 0xDF7C, 0xAF9B, 0xBFBA, 0x8FD9, 0x9FF8, 0x6E17, 0x7E36, 0x4E55, 0x5E74, 0x2E93, 0x3EB2, 0x0ED1, 0x1EF0
};

void usage(void) {
	printf(
	    "rx_rc_telemetry_buf by Rodizio. Based on wifibroadcast rx by Befinitiv. Mavlink code contributed by dino_de. Licensed under GPL2\n"
	    "Hopefully fixes out-of-order packet issues in rx_rc_telemetry\n"
	    "Quick hack that only supports telemetry, no R/C\n"
	    "\n"
	    "Usage: rx_rc_telemetry_buf [options] <interfaces>\n\nOptions\n"
	    "-o <output>     0 = output telemetry and R/C to serialport. 1 = output telemetry to STDOUT, R/C to serialport\n"
	    "-b <baudrate>   Serial port baudrate\n"
	    "-s <serialport> Serial port to use\n"
	    "-r <protocol>   R/C protocol to output. 0 = MSP. 1 = Mavlink. 2 = SUMD. 3 = IBUS. 4 = SRXL/XBUS. 99 = disable R/C\n"
	    "-p <port>       Port for telemetry data. Default = 1\n"
	    "-d <debug>      Debug. Set to 1 for debug output\n"
	    "\n"
	    "Example:\n"
	    "  rx_rc_telemetry_buf -o 0 -b 19200 -s /dev/serial0 -r 0 -p 1 wlan0\n"
	    "\n");
	exit(1);
}

typedef struct {
	pcap_t *ppcap;
	int selectable_fd;
	int n80211HeaderLength;
} monitor_interface_t;

// telemetry frame header consisting of seqnr and payload length
struct header_s {
	uint32_t seqnumber;
	uint16_t length;
}; // __attribute__ ((__packed__)); // not packed for now, doesn't work for some reason
struct header_s header;


struct rcdata_s {
	unsigned int chan1 : 11;
	unsigned int chan2 : 11;
	unsigned int chan3 : 11;
	unsigned int chan4 : 11;
	unsigned int chan5 : 11;
	unsigned int chan6 : 11;
	unsigned int chan7 : 11;
	unsigned int chan8 : 11;
} __attribute__ ((__packed__));
struct rcdata_s rcdata;


long long current_timestamp() {
    struct timeval te;
    gettimeofday(&te, NULL); // get current time
    long long milliseconds = te.tv_sec*1000LL + te.tv_usec/1000; // caculate milliseconds
    return milliseconds;
}


void open_and_configure_interface(const char *name, monitor_interface_t *interface) {
	struct bpf_program bpfprogram;
	char szProgram[512];
	char szErrbuf[PCAP_ERRBUF_SIZE];

	int port_encoded = (param_port * 2) + 1;

	// open the interface in pcap
	szErrbuf[0] = '\0';

	interface->ppcap = pcap_open_live(name, 400, 0, -1, szErrbuf);
	if (interface->ppcap == NULL) {
		fprintf(stderr, "Unable to open %s: %s\n", name, szErrbuf);
		exit(1);
	}
	
	if(pcap_setnonblock(interface->ppcap, 1, szErrbuf) < 0) {
		fprintf(stderr, "Error setting %s to nonblocking mode: %s\n", name, szErrbuf);
	}

	int nLinkEncap = pcap_datalink(interface->ppcap);

	// match (RTS BF) or (DATA, DATA SHORT, RTS (and port))
	if (nLinkEncap == DLT_IEEE802_11_RADIO) {
	    if (param_rc_protocol != 99) { // only match on R/C packets if R/C enabled
		sprintf(szProgram, "ether[0x00:4] == 0xb4bf0000 || ((ether[0x00:2] == 0x0801 || ether[0x00:2] == 0x0802 || ether[0x00:4] == 0xb4010000) && ether[0x04:1] == 0x%.2x)", port_encoded);
	    } else {
		sprintf(szProgram, "(ether[0x00:2] == 0x0801 || ether[0x00:2] == 0x0802 || ether[0x00:4] == 0xb4010000) && ether[0x04:1] == 0x%.2x", port_encoded);
	    }
	} else {
		fprintf(stderr, "ERROR: unknown encapsulation on %s! check if monitor mode is supported and enabled\n", name);
		exit(1);
	}

	if (pcap_compile(interface->ppcap, &bpfprogram, szProgram, 1, 0) == -1) {
		puts(szProgram);
		puts(pcap_geterr(interface->ppcap));
		exit(1);
	} else {
		if (pcap_setfilter(interface->ppcap, &bpfprogram) == -1) {
			fprintf(stderr, "%s\n", szProgram);
			fprintf(stderr, "%s\n", pcap_geterr(interface->ppcap));
		} else {
		}
		pcap_freecode(&bpfprogram);
	}

	interface->selectable_fd = pcap_get_selectable_fd(interface->ppcap);
}


void receive_packet(monitor_interface_t *interface, int adapter_no) {
    struct pcap_pkthdr * ppcapPacketHeader = NULL;
    struct ieee80211_radiotap_iterator rti;
    PENUMBRA_RADIOTAP_DATA prd;
    u8 payloadBuffer[300];
    u8 *pu8Payload = payloadBuffer;
    int bytes;
    int n;
    int retval;
    int u16HeaderLen;
    int type = 0; // r/c or telemetry
    int dbm_tmp;

    retval = pcap_next_ex(interface->ppcap, &ppcapPacketHeader, (const u_char**)&pu8Payload); // receive
    if (retval < 0) {
	if (strcmp("The interface went down",pcap_geterr(interface->ppcap)) == 0) {
	    fprintf(stderr, "rx: The interface went down\n");
	    exit(9);
	} else {
	    fprintf(stderr, "rx: %s\n", pcap_geterr(interface->ppcap));
	    exit(2);
	}
    }
    if (retval != 1) return;

    // fetch radiotap header length from radiotap header (seems to be 36 for Atheros and 18 for Ralink)
    u16HeaderLen = (pu8Payload[2] + (pu8Payload[3] << 8));
//  fprintf(stderr, "u16headerlen: %d\n", u16HeaderLen);

    pu8Payload += u16HeaderLen;
    switch (pu8Payload[1]) {
    case 0xbf: // rts (R/C)
//	fprintf(stderr, "rts R/C frame\n");
        interface->n80211HeaderLength = 0x04;
	type = 0;
        break;
    case 0x01: // data short, rts (telemetry)
//	fprintf(stderr, "data short or rts telemetry frame\n");
        interface->n80211HeaderLength = 0x05;
	type = 1;
        break;
    case 0x02: // data (telemetry)
//	fprintf(stderr, "data telemetry frame\n");
        interface->n80211HeaderLength = 0x18;
	type = 1;
        break;
    default:
        break;
    }
    pu8Payload -= u16HeaderLen;

//  fprintf(stderr, "ppcapPacketHeader->len: %d\n", ppcapPacketHeader->len);
    if (ppcapPacketHeader->len < (u16HeaderLen + interface->n80211HeaderLength)) exit(1);

    bytes = ppcapPacketHeader->len - (u16HeaderLen + interface->n80211HeaderLength);
    if (param_debug == 1) fprintf(stderr, "len:%d ", bytes);
    if (bytes < 0) exit(1);

    if (ieee80211_radiotap_iterator_init(&rti, (struct ieee80211_radiotap_header *)pu8Payload, ppcapPacketHeader->len) < 0) exit(1);

    while ((n = ieee80211_radiotap_iterator_next(&rti)) == 0) {
	switch (rti.this_arg_index) {
	    case IEEE80211_RADIOTAP_FLAGS:
		prd.m_nRadiotapFlags = *rti.this_arg;
		break;
	    case IEEE80211_RADIOTAP_DBM_ANTSIGNAL:
//		fprintf(stderr, "ant signal:%d\n",(int8_t)(*rti.this_arg));
//		rx_status->adapter[adapter_no].current_signal_dbm = (int8_t)(*rti.this_arg);
		dbm_tmp = (int8_t)(*rti.this_arg);
		break;
	}
    }

    if (param_debug == 1) fprintf(stderr, "dbm:%d ", dbm_tmp);

    rx_status->adapter[adapter_no].current_signal_dbm = dbm_tmp;
    rx_status->adapter[adapter_no].received_packet_cnt++;
    rx_status->last_update = time(NULL);
    dbm_tmp = 0;
    pu8Payload += u16HeaderLen + interface->n80211HeaderLength;
    memcpy(&header,pu8Payload,6); //copy header (seqnum and length) to header struct
    pu8Payload += 6;

    int already_received = 0;
    int t;
    for (t=0;t<100;t++) {
	if (buffer[t].seq == header.seqnumber) { // seqnum has already been received
	    already_received = 1;
//	    fprintf(stderr,"already received\n");
	}
    }

    if ((already_received == 0) && (header.seqnumber > lastseq)) {
	int y;
	int done = 0;
	    for (y=0;y<100;y++) {
		if (buffer[y].filled == 0) { // buffer is empty, use it
		    memcpy(buffer[y].payload,pu8Payload,header.length);
		    buffer[y].len = header.length;
		    buffer[y].seq = header.seqnumber;
		    buffer[y].filled = 1;
		    if (param_debug == 1) fprintf(stderr,"seq %d->buf[%d] ",buffer[y].seq,y);
		    done = 1;
		} else {
		    //fprintf(stderr,"buffer[%d] already filled\n",y);
		}
		if (done == 1) {
		    //fprintf(stderr,"done!\n");
		    break;
		}
	    }
	    if (done == 0) { // no empty buffer found, we just use a filled one
		int randomnum = rand() % 100;
		memcpy(buffer[randomnum].payload,pu8Payload,header.length);
		buffer[randomnum].len = header.length;
		buffer[randomnum].seq = header.seqnumber;
		buffer[randomnum].filled = 1;
		if (param_debug == 1) fprintf(stderr,"FULL! seq %d->buf[%d] ",buffer[randomnum].seq,randomnum);
	    }

    } else {
	if (param_debug == 1) fprintf(stderr,"seq %d dupe ",header.seqnumber);
    }

}


void status_memory_init(wifibroadcast_rx_status_t *s) {
	s->received_block_cnt = 0;
	s->damaged_block_cnt = 0;
	s->received_packet_cnt = 0;
	s->lost_packet_cnt = 0;
	s->tx_restart_cnt = 0;
	s->wifi_adapter_cnt = 0;
	s->kbitrate = 0;

	int i;
	for(i=0; i<8; ++i) {
		s->adapter[i].received_packet_cnt = 0;
		s->adapter[i].wrong_crc_cnt = 0;
		s->adapter[i].current_signal_dbm = 0;
	}
}


wifibroadcast_rx_status_t *status_memory_open(void) {
	char buf[128];
	int fd;
	
	sprintf(buf, "/wifibroadcast_rx_status_%d",param_port);
	fd = shm_open(buf, O_RDWR, S_IRUSR | S_IWUSR);
	if(fd < 0) {
		perror("shm_open"); exit(1);
	}
//	if (ftruncate(fd, sizeof(wifibroadcast_rx_status_t)) == -1) {
//		perror("ftruncate"); exit(1);
//	}
	void *retval = mmap(NULL, sizeof(wifibroadcast_rx_status_t), PROT_READ | PROT_WRITE, MAP_SHARED, fd, 0);
	if (retval == MAP_FAILED) {
		perror("mmap"); exit(1);
	}
	wifibroadcast_rx_status_t *tretval = (wifibroadcast_rx_status_t*)retval;
	status_memory_init(tretval);
	return tretval;
}

wifibroadcast_rx_status_t *status_memory_open_rc(void) {
	char buf[128];
	int fd;
	
	sprintf(buf, "/wifibroadcast_rx_status_rc");
	fd = shm_open(buf, O_RDWR, S_IRUSR | S_IWUSR);
	if(fd < 0) {
		perror("shm_open"); exit(1);
	}
//	if (ftruncate(fd, sizeof(wifibroadcast_rx_status_t)) == -1) {
//		perror("ftruncate"); exit(1);
//	}
	void *retval = mmap(NULL, sizeof(wifibroadcast_rx_status_t), PROT_READ | PROT_WRITE, MAP_SHARED, fd, 0);
	if (retval == MAP_FAILED) {
		perror("mmap"); exit(1);
	}
	wifibroadcast_rx_status_t *tretval = (wifibroadcast_rx_status_t*)retval;
	status_memory_init(tretval);
	return tretval;
}



int main(int argc, char *argv[]) {
	printf("RX R/C Telemetry_buf started\n");

	srand(time(NULL));

	long long prev_time = 0;
	long long delta = 0;

	monitor_interface_t interfaces[8];
	int i, p, serialport, num_interfaces = 0;

	int writefailcounter, writesuccess, atleastonebufferfilled, lostpackets, nothing_received_cnt = 0;
	int abuffers_filled = 0;


	for (p=0;p<100;p++) {
	    buffer[p].filled = 0;
	    buffer[p].seq = 0;
	}

	while (1) {
		int nOptionIndex;
		static const struct option optiona[] = { { "help", no_argument, &flagHelp, 1 }, { 0, 0, 0, 0 } };
		int c = getopt_long(argc, argv, "h:o:b:s:r:p:d:", optiona, &nOptionIndex);
		if (c == -1)
			break;
		switch (c) {
		case 0: // long option
			break;
		case 'h': // help
			usage();
		case 'o': // output
			param_output = atoi(optarg);
			break;
		case 'b': // baudrate
			param_baudrate = atoi(optarg);
			break;
		case 's': // serialport
			param_serialport = optarg;
			break;
		case 'r': // R/C protocol
			param_rc_protocol = atoi(optarg);
			break;
		case 'p': // port
			param_port = atoi(optarg);
			break;
		case 'd': // debug
			param_debug = atoi(optarg);
			break;
		default:
			fprintf(stderr, "unknown switch %c\n", c);
			usage();
		}
	}
	if (optind >= argc) usage();
	int x = optind;
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

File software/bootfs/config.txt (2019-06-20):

# For more options and information see
# http://rpf.io/configtxt
# Some settings may impact device functionality. See link above for details

# uncomment if you get no picture on HDMI for a default "safe" mode
#hdmi_safe=1

# uncomment this if your display has a black border of unused pixels visible
# and your display can output without overscan
#disable_overscan=1

# uncomment the following to adjust overscan. Use positive numbers if console
# goes off screen, and negative if there is too much border
#overscan_left=16
#overscan_right=16
#overscan_top=16
#overscan_bottom=16

# uncomment to force a console size. By default it will be display's size minus
# overscan.
#framebuffer_width=1280
#framebuffer_height=720

# uncomment if hdmi display is not detected and composite is being output
#hdmi_force_hotplug=1

# uncomment to force a specific HDMI mode (this will force VGA)
#hdmi_group=1
#hdmi_mode=1

# uncomment to force a HDMI mode rather than DVI. This can make audio work in
# DMT (computer monitor) modes
#hdmi_drive=2

# uncomment to increase signal to HDMI, if you have interference, blanking, or
# no display
#config_hdmi_boost=4

# uncomment for composite PAL
#sdtv_mode=2

#uncomment to overclock the arm. 700 MHz is the default.
#arm_freq=800

# Uncomment some or all of these to enable the optional hardware interfaces
#dtparam=i2c_arm=on
#dtparam=i2s=on
#dtparam=spi=on

# Uncomment this to enable the lirc-rpi module
#dtoverlay=lirc-rpi

# Additional overlays and parameters are documented /boot/overlays/README

# Enable audio (loads snd_bcm2835)
#dtparam=audio=on

dtoverlay=pi3-disable-bt
gpu_mem=256
enable_uart=1
#start_x=1

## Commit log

2019-02-11 Added antenna segment 3d print files.
    Added the SLDPRT and STL files of the helical antenna (initial version). Also added initial version of README files for the associated folders.
    [Antenna_Segment.SLDPRT]
2019-02-11 Improved helical antenna 3d model, fixed helix direction
    Flipped helix direction from left hand to right hand.
    Widened peg holes from 5.1 to 5.5.
    Chamfered peg holes to counteract first layer smooshing.
    Moved pegs and peg holes closer to exterior, from a 20mm diameter circle to 24mm.
    [Antenna_Segment.SLDPRT]
2019-02-11 Improved helical antenna 3d model to disallow incorrect assembly
    Converted a peg to a 'key' peg to disallow incorrect rotation.
    [Antenna_Segment.SLDPRT]
2019-02-12 Helical antenna model, enlarged pegs, added anchor trough at top
    Cut number of pegs to three, enlarged remaining pegs.
    Added trough for anchoring the wire at the top of the antenna.
    [Antenna_Segment.SLDPRT]
2019-02-26 Reorganized 3d model folders, changed antenna pegs to square.
    Reorganized 3D models into one folder, with added documentation, to support a mockup assembly.
    Replaced previous three round pegs with a single square peg with an alignment peg attached to one side. Should allow for a single top cap that can be attached in four orientations for the 4 antenna array.
    [Antenna_Segment.SLDPRT, Helical_Antenna_Segment.SLDPRT]
2019-02-28 Removed old Rpi model, added several new models. Added HGS assembly.
    Added new Raspberry Pi Zero model found online, with attribution.
    Made several new models for the backplane, phone holder, antella endcap, and a few simple box stand in models for parts I don't know the exact shape for.
    Made an assembly showing all the component put together into an example Handheld Ground Station.
    [Antenna_Endcap.SLDPRT, Atheros_Dummy.SLDPRT, Backplane.SLDPRT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]
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2019-04-07 Updated readme dimensions, added handle, added spacers for phone holder
    Also modified phone holder base to use spacers.
    [Handle.SLDPRT, Handle_Clamp.SLDPRT, Phone_Holder_Base.SLDPRT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]
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2019-04-27 Handle model: smoothed edges, added 1/4-20 nut slot for mounting, etc.
    Added screw insets for the clamp.
    Added exported model for printing.
    [Handle.SLDPRT]
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2019-04-27 Antenna_endcap: changed name to "Antenna_Base_Clamp", etc
    Made clamp tighter (to size of peg without extra clearance.)
    Added .stl for printing.
    [Antenna_Base_Clamp.SLDPRT, Antenna_Base_Clamp.STL, Antenna_Endcap.SLDPRT]
2019-04-27 Phone_holder_spacer removed and integrated into phone_holder_base
    Added screw head insets to top
    [Phone_Holder_Base.SLDPRT, Phone_Holder_Base.STL, Phone_Holder_Spacer.SLDPRT]
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2019-04-27 Phone_holder_clamp: Added rear rail for clamping, and misc
    Added .stl copy for printing.
    Fixed screw inset size.
    Adjusted things a bit to ease accessing screw holes on inside.
    [Phone_Holder_Clamp.SLDPRT, Phone_Holder_Clamp.STL]
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2019-04-27 Added Antenna_Cap, and .stl version for printing, fixed typo in readme
    [Antenna_Cap.SLDPRT, Antenna_Cap.STL]
2019-04-29 Made most of the backplane design, no idea if it'll actually work
    Missing impedance matching bit
    [backplane.kicad_pcb, backplane.sch]
2019-04-29 Fixed folder structure of KiCad backplane bits
    Made an oopsie getting used too new software.
    [backplane.kicad_pcb, backplane.sch]
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2019-04-30 Fixed reference to footprint library location
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2019-05-01 Changed microstrip and added clearance
    Also removed a giant SMD pad in footprint for antenna.
    [backplane.kicad_pcb]
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2019-05-01 Updated footprint and PCB layout
    Accidently undid a new through-hole in last commit.
    Updated footprint for microstrip to include clearance.
    [backplane-B_Cu.gbr, backplane-B_Mask.gbr, backplane-B_Paste.gbr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]
2019-05-08 Updated microstrip and moved components around
    Microstrip now has solder mask on the tips for soldering wires to it,
    and holes nearby for connecting coax cable and antenna.
    RPi and WiFi module mount holes have been moved to match first prototype
    assembled for open house.
    [backplane.kicad_pcb]
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2019-05-09 Updated silkscreen and REF values for footprints
    Footprints now have unique names for easy reference in library.
    Names for footprints have been moved around so that they don't overlap
    on PCB layout.
    Labels for RPi Zero connections moved outside box for visibility when
    RPi is mounted onto backplane.
    [backplane.kicad_pcb]
2019-05-09 Split handle into two halves, added battery compartment, etc.
    Added bolt holes and etc. for attaching halves together.
    Added slot for USB cables for battery.
    Changed bolt hole diameter from 3mm to 3.2mm as part of future project wide change.
    Changed bolt head inset diameter from 7.5mm to 6.5mm
    Removed Full handle .stl file, and added .stl files for the halves. (battery compartment would be inaccessible if printed as one part.)
    [Handle.SLDPRT, Handle_Bottom.SLDPRT, Handle_Top.SLDPRT]
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2019-05-09 Added OreSat logo to silkscreen
    Included dxf version of logo needed to import to Kicad
    Added logo as footprint (includes version number)
    [backplane.kicad_pcb, oresat.dxf]
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2019-05-13 Added holes for strings and modified microstrip
    Board layout now reflects what users see when using the product from the
    back of the board. The side of the microstrip where the antenna will feed
    in now has a rectangular hole.
    [backplane.kicad_pcb]
2019-05-13 Moved transformer slot to be tangent with antenna slot
    Adjusted slot so that it lines up with where the antenna wire ends for
    nice flow for wire to feed through.
    Also changed mount holes to be full 3mm mechanical drill holes for the
    following footprints:
    - Handle Clamp
    - Phone Holder
    [backplane.kicad_pcb]
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2019-05-13 Connected GND planes using vias with common net
    Added new footprint linked with net from two floating inductors in schematic
    to associate both planes and all vias to connect everything together.
    [backplane.kicad_pcb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]
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2019-05-16 Handle: suppressed features, shortened handle (reverting to no battery)
    Suppressed USB slot
    Suppressed battery compartment
    Shortened handle back to previous length for more solid assembly
    Made bolt holes slightly larger
    Chamfered bolt head insets for printing
    Filleted handle top corners
    [Handle.SLDPRT, Handle_Bottom.SLDPRT, Handle_Top.SLDPRT]
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2019-05-17 Flipped layers for all components
    The layer with silkscreen outlines for components is supposed to represent
    what users should see when holding HGS. This should be on the front layer
    so that placement doesn't get flipped when it's on the back.
    [backplane.kicad_pcb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]
2019-05-25 Adding major changes to transformer and others
    Moved Atheros module out from under phone clamp for easier assembly.
    Slot for antenna wire to feed through is now a edge cut.
    Through-hole to GND plane on opposite end of transformer is now a SMD for
    a UFL connector.
    Transformer clearance is now a copper trace isolating the microstrip.
    [backplane.kicad_pcb]
2019-05-25 Disconnected transformer clearance border from microstrip
    Gerber files have also been updated to reflect the current layout
    [backplane-B_Cu.gbr, backplane-B_Mask.gbr, backplane-B_Paste.gbr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]
2019-05-26 Changed antenna feed slot width to be 1.5mm and other
    Cleaned up floating unnecessary silkscreen
    Removed solder mask for mounting holes
    Updated version number text for HGS
    [backplane.kicad_pcb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]
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2019-05-28 Handle/split handle: updated fastener sizes to new standard
    Also enlarged standard sizes slightly
    [Handle.SLDPRT, Handle_Bottom.SLDPRT, Handle_Top.SLDPRT]
2019-05-28 Handle clamp: updated to new fastener standard
    Also added forgotten update to standard made last push
    [Handle_Clamp.SLDPRT, Handle_Clamp.STL]
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2019-05-29 Shifted transformer 1mm to the side and 3mm downward
    Transformer was moved so that there is a smoother transition for the
    antenna wire to feed to the back of the board.
    [backplane.kicad_pcb]
2019-05-29 Replaced transformer isolation with "Keep Out" zones
    Was previously using a copper trace to isolate the transformer to prevent
    copper fill to get around it. Found keep out zone option to define areas
    that we don't want copper to be in.
    [backplane-B_Cu.gbr, backplane-B_Mask.gbr, backplane-B_Paste.gbr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]
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2019-06-02 Adding major final changes for transformer strip
    Moved transformer parts closer to antenna by 1mm
    Transformer microstrip reverted to original intended size
    Added footprint for 0402 capacitor to replace gap between U.FL and strip
    Modified U.FL footprint pads to be "solid" to allow for copper fill to
    connect to the GND pads
    Phone Clamp and Handle mount holes changed to 4.5mm
    Fixed README text hyperlink for footprint dimension references
    Removed unused/blank footprints in Kicad library
    [backplane-B_Cu.gbr, backplane-B_Mask.gbr, backplane-B_Paste.gbr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]
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2019-06-02 Update Phone Holder footprint to new design
    Holes are now 50mm apart horizontally and 90mm vertically
    Fixed hyperlinking text for README
    [backplane-B_Cu.gbr, backplane-B_Mask.gbr, backplane-B_Paste.gbr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]
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2019-06-21 Removed Kicad temp and unecessary files
    Added gitignore to prevent pushes of temp files
    [oresat.dxf]
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2020-07-19 Fixed sch/brd inconsistancy
    [HGS_Reflector.brd, HGS_Reflector.sch]
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2020-08-02 Fixed USB pin issue
    [HGS_Reflector.sch]
2020-08-02 Fixed USB A port name
    [HGS_Reflector.sch]
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2020-08-16 Fixed consistency errors by blowing away board and recreating from previous version.
    [HGS_Reflector.brd, HGS_Reflector.sch]
2020-08-18 Correcting the file name for the BOM
    [Handhled Ground Station BOM.xlsx]
2020-08-18 Quick fix with the folders.
    [Handheld Ground Station BOM.xlsx]
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2020-10-06 Fixed a bad cut.
    [Phone&BatteryHolderBottom.SLDPRT]
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2020-10-18 I completed the physical layout of the board for HGS. Currently, I just need to sort through some DRC errors that I don't know how to fix, and do a design review.
    [HGS_Reflector.brd, HGS_Reflector.sch]
2020-10-18 For the HGS board, I fixed some DRC clearance errors.
    [HGS_Reflector.brd]
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2020-12-06 Fixed hex trap CAD
    [HelicalAntennaSegmentCap.SLDPRT, HelicalAntennaSegments.SLDPRT, Phone&BatteryHolderBottom.SLDPRT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]
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2020-12-11 Cleanup of mechanical stuff; rotated board, imported DXF, reset the dim layer, and put grounds on all layers.
    [HGS_Reflector.brd]
2020-12-12 With the DXF layer properly configured, I positioned all parts onto the board and completed all of the routing. However, there are a few DRC issues involving details of footprints that need to be cha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
    [HGS_Reflector.brd, HGS_Reflector.sch]
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2020-12-13 I made sure that all the signals were completely routed, and fixed the clearance issue with the wire going to the center by replacing the center drill hole with a large via that goes directly to the 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
    [HGS_Reflector.brd, HGS_Reflector.sch]
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2020-12-22 Fixed tolerance issue with hex trap and various other parts
    [HelicalAntennaSegmentCap.SLDPRT, HelicalAntennaSegments.SLDPRT, Phone&BatteryHolderBase.SLDPRT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]
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2020-12-23 Fixed keepout zones, removed antenna through hole, put 1/4 wave transformer in the right place, but, this is going to be totally hoky. Is there a better way?
    [HGS_Reflector.brd, HGS_Reflector.sch]
2020-12-23 Added antenna side DXF and fixed broken assembly relations
    [keepoutAntennaSide.DXF]
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2020-12-25 After connecting the Pi 0W footprint to the ground plane, I fixed the issue of the Pi 0W pin header floating.
    [HGS_Reflector.brd, HGS_Reflector.sch]
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2021-01-30 Made changes in CAD for clearance and ease of assembly, changed threaded rods to aluminium, and removed unnecessary files
    [90480A009_LOW-STRENGTH STEEL HEX NUT.SLDPRT, 91115A831_18-8 SS FEM THRDED HEX STANDOFF.SLDPRT, 91565A335_LOW-STRENGTH STEEL THREADED ROD.SLDPRT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]
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2022-04-19 sweaks to sma connector footprint to unbork the errors from the eagle port
    [billofmaterials.xls, transformer.kicad_pcb]
2022-04-21 Fixed .gitignore for KiCAD 6, removed backups and other temp files, updated board file with 4 layer oshpark from the oresat-kicad repo, moved antenna much closer to the transformer and reduced the tr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
    [transformer.kicad_pcb]
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2022-04-21 fixed SMA connector footprint, moved text from paste to silk layer
    [transformer.kicad_pcb, transformer.kicad_sch]
2022-04-21 Sent off for Fab, v1.0
    Updated libraries and library paths; might actually not be terrible now with the submodule? Fixed footprint of transformer and rotated 90 degrees; made board OCD compliant and did via cleanup.
    [transformer.kicad_pcb, transformer.kicad_sch]
2022-04-21 Stackup was wrong; didn't update when importing DRU template file. Fixed manually. Doesn't affect Gerbers or drill files.
    [transformer.kicad_pcb]
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2022-05-01 LNA
    Fixed minor issues in RF path.
    [LNA.kicad_pcb, LNA.kicad_sch]
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2022-07-10 fixed microstrip width and moved SMA away from R1
    [HGS_antenna_tester.kicad_pcb]
2022-07-10 added missing antenna form mounting holes
    [HGS_antenna_tester.kicad_pcb]
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2022-07-18 stictching and typo fixes
    [HGS_antenna_tester.kicad_pcb, HGS_antenna_tester.kicad_sch]
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2023-05-23 Fixed vias and ground plane
    moved some vias around and fixed the ground plane around the stub to follow the 3W rule.
    [50_ohm_microstrip_experiment.kicad_pcb, 50_ohm_microstrip_experiment.kicad_sch]
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2023-05-26 Fixed issues with backside SMA connector GND pins
    backside GND pins had not net. Connected them to GND net
    [50_ohm_microstrip_experiment.kicad_pcb]
2023-05-26 Added designators and fixed soldermask removal
    Added designators and fixed soldermask removal
    Also added board title
    [50_ohm_microstrip_experiment.kicad_pcb]
2024-07-29 replaced some eagle import symbols with kicad symbols
    [HGS_Reflector.kicad_sch]
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2024-09-13 fixed reference designators, fixed symbol/footprint pads and pins, added impedance matching at helical
    [HGS_Reflector.kicad_pcb, HGS_Reflector.kicad_sch]
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

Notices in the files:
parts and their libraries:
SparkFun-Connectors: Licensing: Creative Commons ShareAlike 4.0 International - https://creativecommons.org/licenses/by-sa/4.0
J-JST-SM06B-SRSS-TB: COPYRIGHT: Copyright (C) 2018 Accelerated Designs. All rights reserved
